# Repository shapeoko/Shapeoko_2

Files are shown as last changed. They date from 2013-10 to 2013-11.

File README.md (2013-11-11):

####Shapeoko is as much an idea as a physical machine.####

An idea that maybe there are people like me in the world. An idea that some people want a CNC machine but don't want to spend thousands of dollars to get one. An idea that maybe there are people who want a CNC machine, but don't necessarily know what they will make. An idea that maybe there are people who want a CNC machine but don't know how to use a CNC machine! An idea that maybe there are people who want to build something that was their own hands, but are not expert fabricators. An idea that a machine could be designed that was hackable, scalable, customizable, but doesn't require the re-invention of the wheel for each modification.

####An idea that maybe there was a different way to do CNC.####

Those ideas laid the foundation for Project Shapeoko. It was those ideas that [the community](http://www.shapeoko.com/forum) has built itself around. A community that started out as an email list and is now 1000+ active members strong, and growing everyday. A community that I wouldn't trade for anything.

Over the last two years the community has bounced ideas off each other, tested new ideas, discussed and debated trade-offs in various designs and improvements, and helped each other make a better machine. We are a pragmatic, positive bunch that hasn't taken it's eye off the main goal of the project: Let's do CNC a different way. Let's commoditize it, let's make it accessible to anyone who wants it, and lets give anyone a place where they can come learn, a place they can be part of a community, and place where the newest, greenest, most inexperienced person's ideas and suggestions are taken as seriously as anyone elses. 

Maybe the project is a physical Machine, but it's the community that keeps the project together. It's the community that keeps the project moving forward, and it's the community that is responsible for Shapeoko 2.

The culmination of all that, is what you see here. I'd like to introduce you to Shapeoko 2. Say hello.

Shapeoko 2

Shapeoko 2 has taken all of our design improvements and rolled them up into one thoughtful, low-cost, scalable, hackable, simple, beautifully designed package full of improvements over the v1 Release.

####Specifications:####
+ Working area is expanded to about 12" by 12" by 2.5"
+ Open front and back for loading in longer pieces of material
+ Dual-drive motors on the Y axis, standard
+ Double width Makerslide on the X axis for added stiffness and strength
+ Completely redesigned Z axis for added stiffness and easier tool changes
+ The wasteboard is now integrated with the machine
+ Re-engineered belt system keeps teeth cleaner and reduces skipping
+ Easier to assemble- put it together over a weekend or a couple of nights

#####To-Do List#####
- [x] Publish Original Design Files (Autodesk Inventor)
- [x] Publish Generic Design Files (STEP Format)
- [x] Publish Original Drawing Files (Autodesk Inventor)
- [ ] Publish Generic Drawing Files (PDF Format)
- [ ] Publish Generic Drawing Files (DXF Format)
- [X] Publish Assembly Instructions (Outline Format) - WIP
- [ ] Publish Formatted Assembly Instructions

_This is the beginning of this repository. Information will be added as it becomes available and time permits._

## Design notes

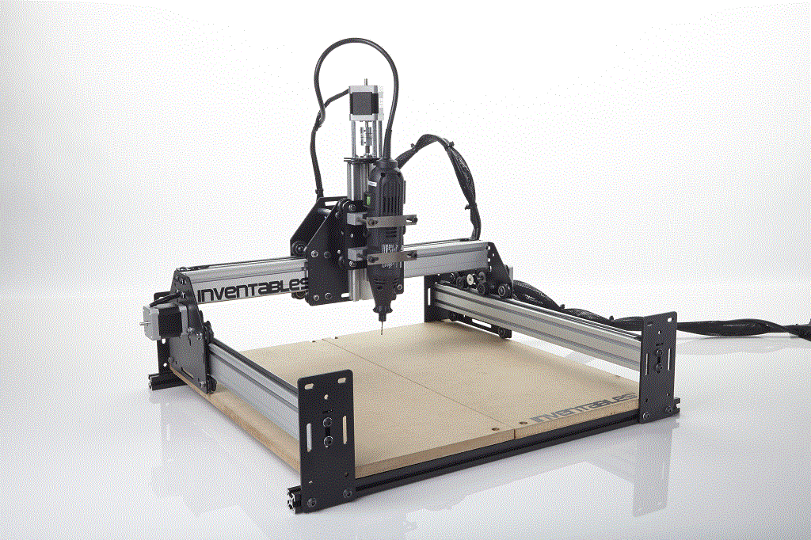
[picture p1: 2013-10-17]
Shapeoko_2.gif

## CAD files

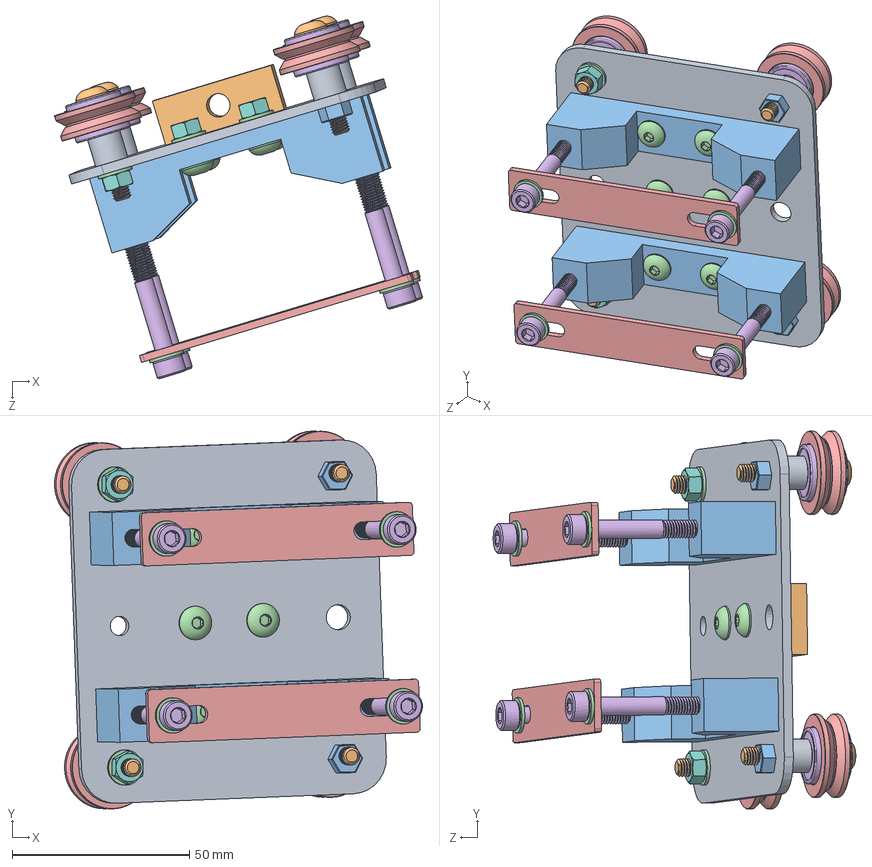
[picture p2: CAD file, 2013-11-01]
SolidWorks_Project/ASM_Zaxis_Trolly.SLDASM
104.0 x 106.7 x 102.4 mm
spindle_mount_plate
SM-M08
B18033 x 2
SM-TM x 2
SM-TM2 x 2
91290A260 x 4

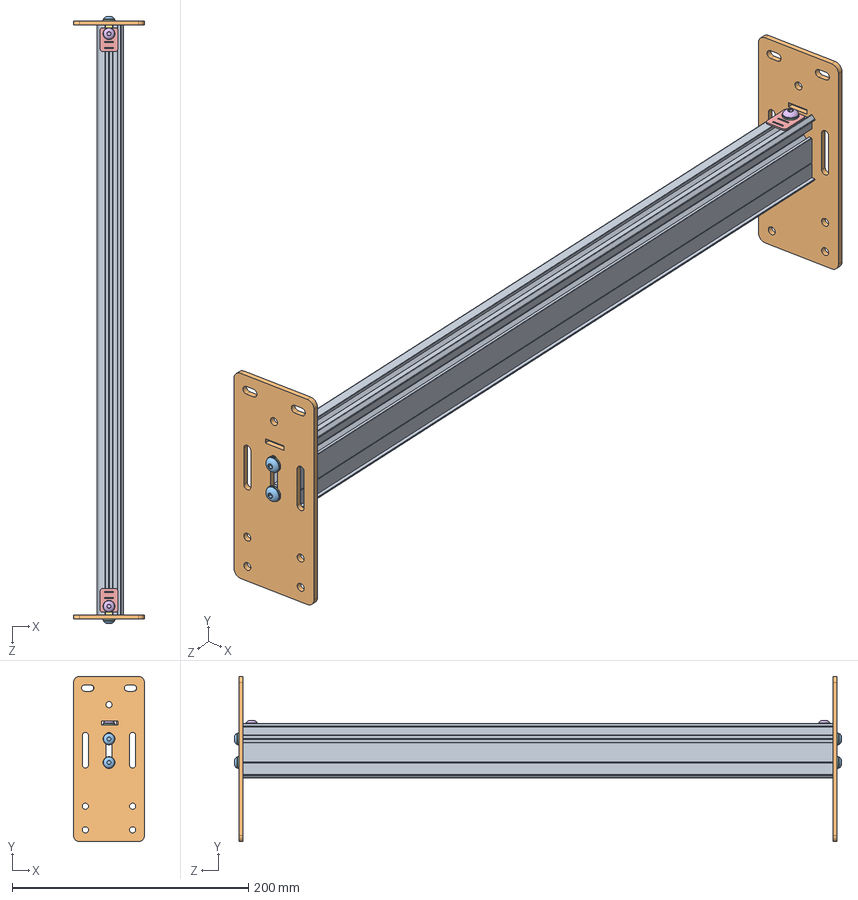
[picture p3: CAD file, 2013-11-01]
SolidWorks_Project/S2_Yaxis_Rail_500.sldasm
60.0 x 140.0 x 514.1 mm
25142-XX500
91239A222 x 2

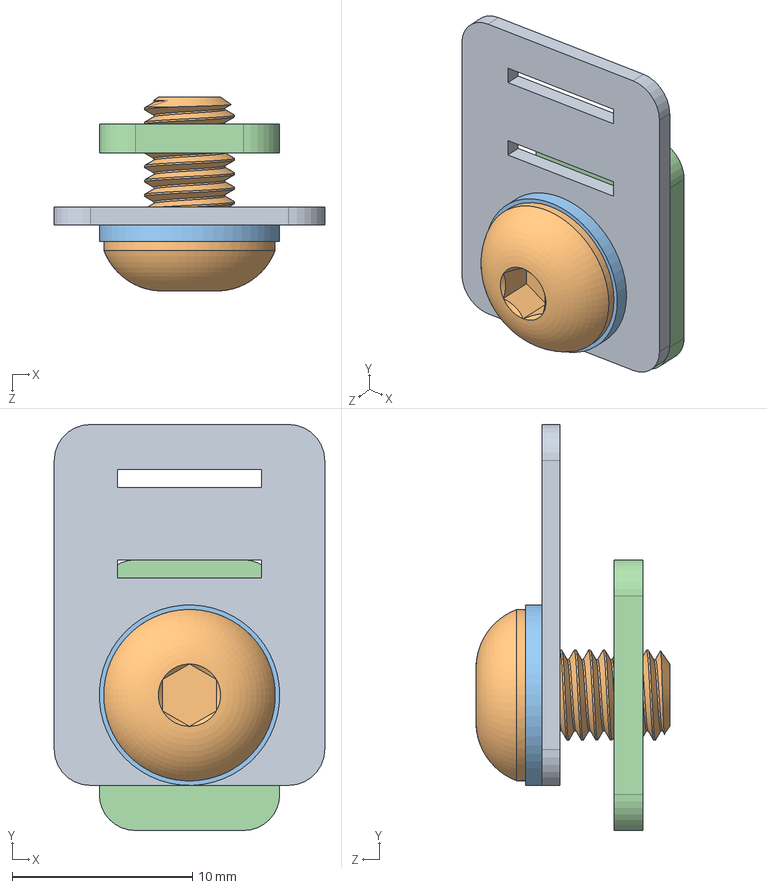
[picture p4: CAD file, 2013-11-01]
SolidWorks_Project/belt_clip_assembly.sldasm
15.0 x 22.5 x 10.7 mm
91239A222

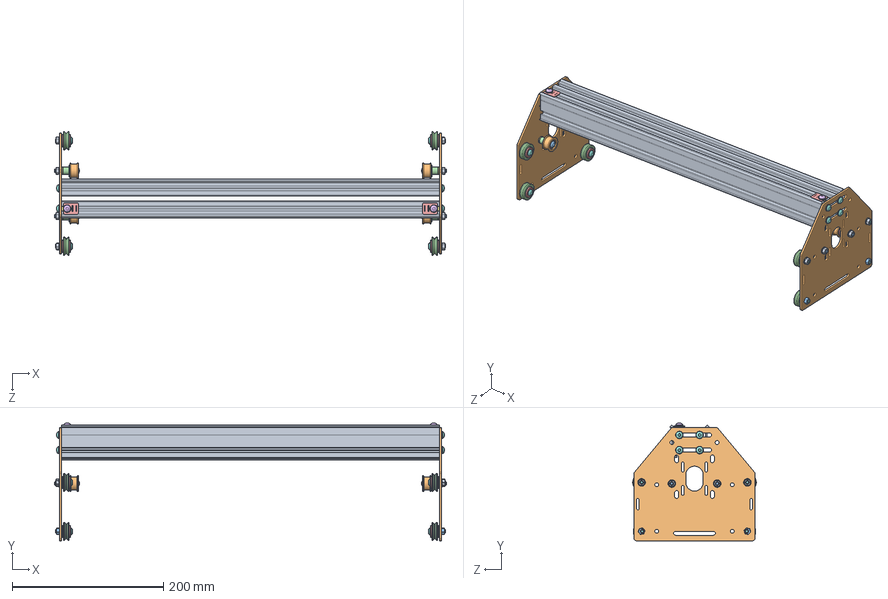
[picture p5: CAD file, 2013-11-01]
SolidWorks_Project/S2_Gantry_500.sldasm
518.5 x 155.6 x 163.5 mm
25142-XX500 x 2
B18033 x 4
91239A233 x 8
91239A222 x 2

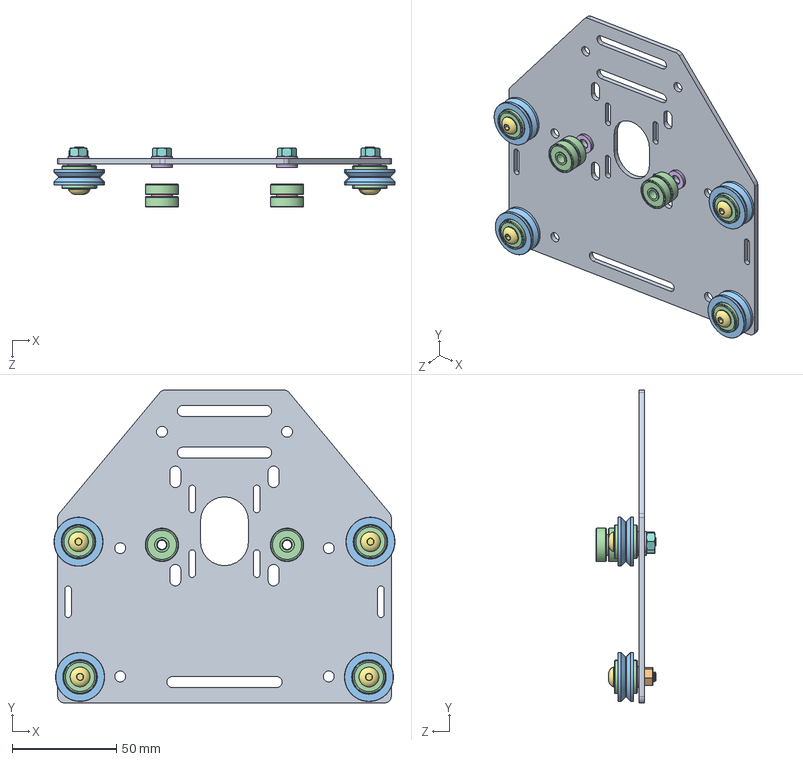
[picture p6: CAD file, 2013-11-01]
SolidWorks_Project/plate_assembly_stacked.sldasm
163.5 x 150.0 x 28.8 mm
B18033 x 2
91239A233 x 4

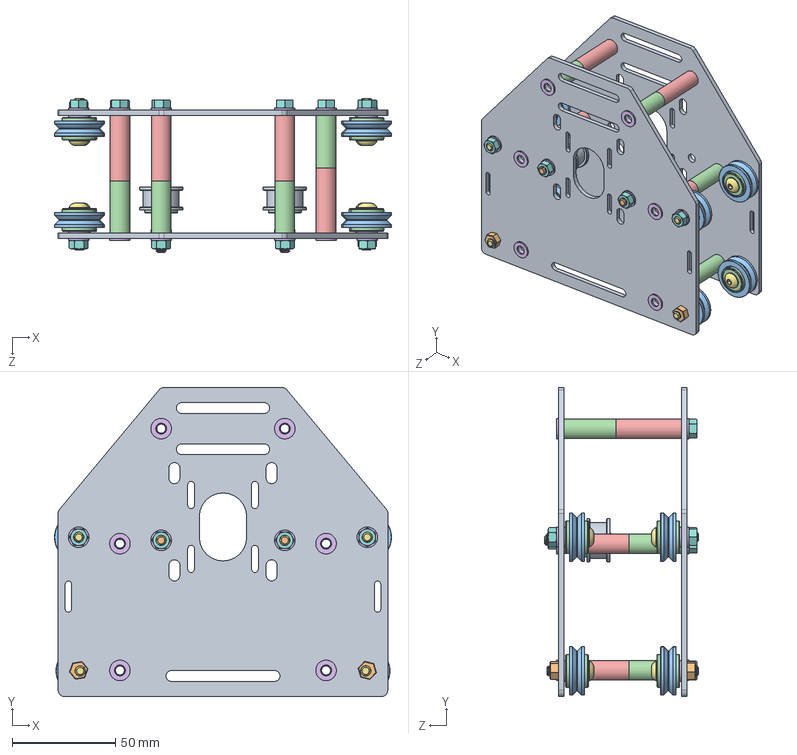
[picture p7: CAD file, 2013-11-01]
SolidWorks_Project/ASM_S2_Yaxis_Plates.SLDASM
163.5 x 150.0 x 74.5 mm
B18033 x 4
91239A233 x 8
AS38-12-64 x 6
AS38-12-80 x 6

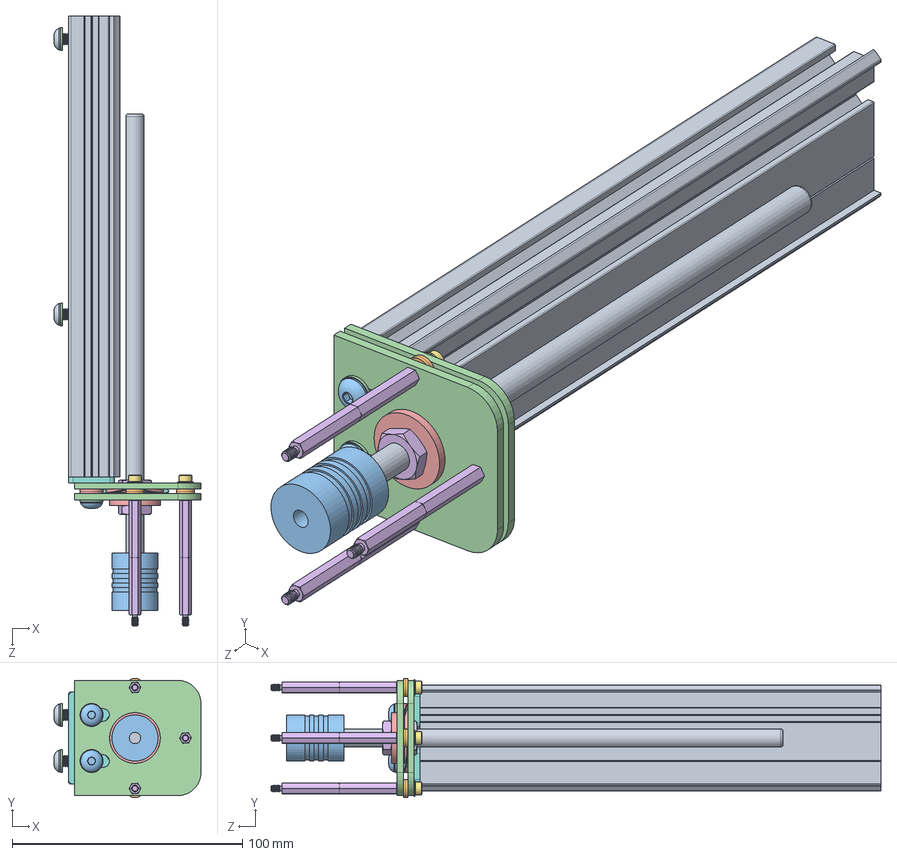
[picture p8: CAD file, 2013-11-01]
SolidWorks_Project/S2_Zaxis_500.sldasm
63.8 x 51.8 x 264.7 mm
z-mount_plates x 2
90695A040 x 2
z-axis shim
SM-H05
492-1101-ND x 6
91239A233 x 2
PSM5-01MM x 4
PSBS-50 x 3
9714K630

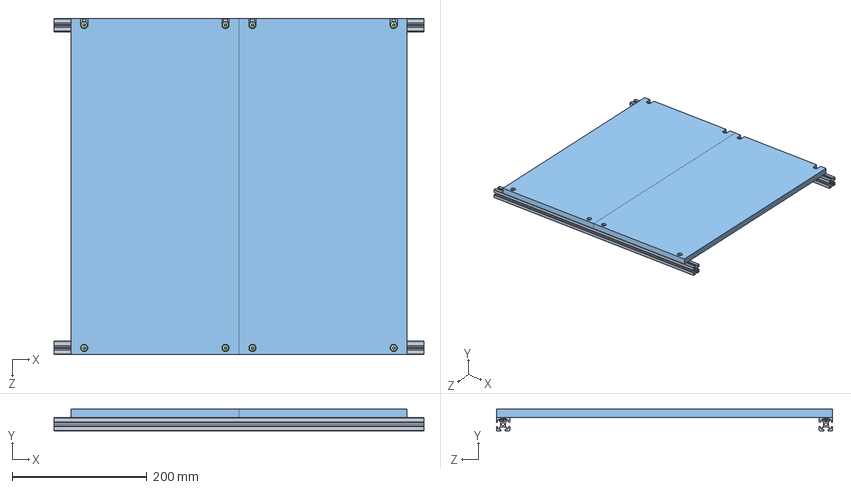
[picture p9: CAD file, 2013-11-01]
SolidWorks_Project/S2_Work_Area_500.sldasm
550.0 x 32.7 x 500.0 mm
two_part_wastebaord_500 x 2

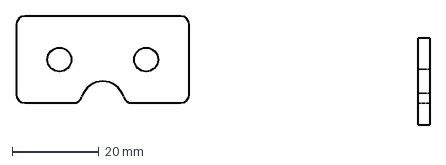
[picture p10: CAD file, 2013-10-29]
Drawings_DXF/SMZS-01.dxf
95.5 x 25.0 mm

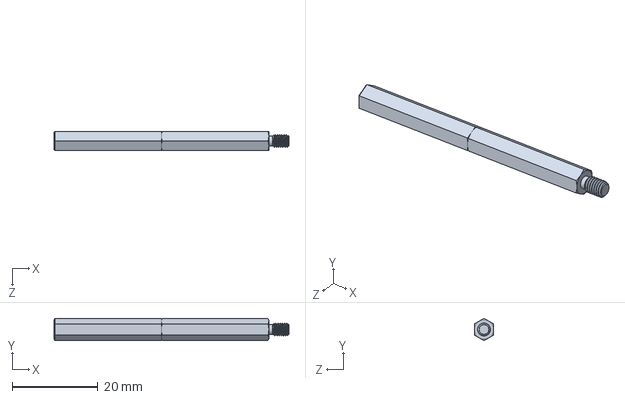
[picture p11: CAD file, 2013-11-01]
SolidWorks_Project/PSBS-50.sldprt
54.7 x 5.20 x 4.50 mm

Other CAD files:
SolidWorks_Project/SM-M08.sldprt
SolidWorks_Project/AS38-12-80.sldprt
SolidWorks_Project/PSM5-01MM.sldprt
SolidWorks_Project/SM-H05.sldprt
SolidWorks_Project/SM-TM.sldprt
SolidWorks_Project/z-axis shim.sldprt
SolidWorks_Project/z-mount_plates.sldprt
SolidWorks_Project/spindle_mount_plate.sldprt
Autodesk_Inventor_Project/25142-07.ipt
Autodesk_Inventor_Project/25142-XX500.ipt
Autodesk_Inventor_Project/25196-01.ipt
Autodesk_Inventor_Project/25197-01.ipt
Autodesk_Inventor_Project/25197-02.iam
Autodesk_Inventor_Project/25201-01.ipt
Autodesk_Inventor_Project/25202-01.ipt
Autodesk_Inventor_Project/25203-02.iam
Autodesk_Inventor_Project/25284-02.ipt
Autodesk_Inventor_Project/25285-10.ipt
Autodesk_Inventor_Project/25286-01.ipt
Autodesk_Inventor_Project/25286-02.ipt
Autodesk_Inventor_Project/25286-05.ipt
Autodesk_Inventor_Project/25287-02.ipt
Autodesk_Inventor_Project/25287-03.ipt
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

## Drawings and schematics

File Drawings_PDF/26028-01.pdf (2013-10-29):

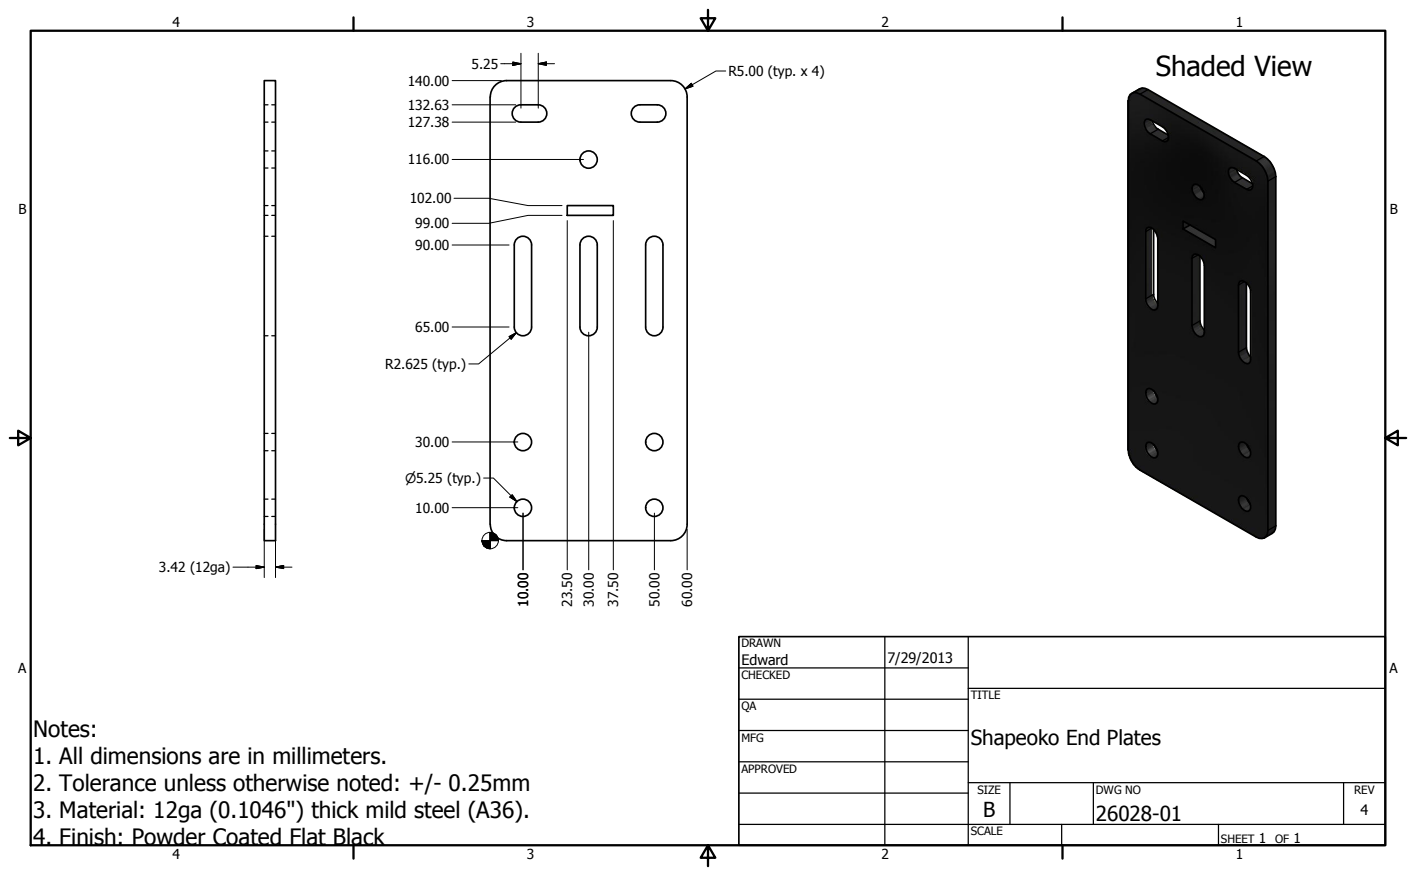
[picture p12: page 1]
SHEET 1 OF 1; DRAWN; CHECKED; MFG; APPROVED; Edward; DWG NO 26028-01; TITLE; SIZE B; SCALE; REV 4; P5.25 (typ.); R2.625 (typ.); R5.00 (typ. x 4); Shaded View

Notes:
1. All dimensions are in millimeters.
2. Tolerance unless otherwise noted: +/- 0.25mm
3. Material: 12ga (0.1046") thick mild steel (A36).
4. Finish: Powder Coated Flat Black

Shapeoko End Plates

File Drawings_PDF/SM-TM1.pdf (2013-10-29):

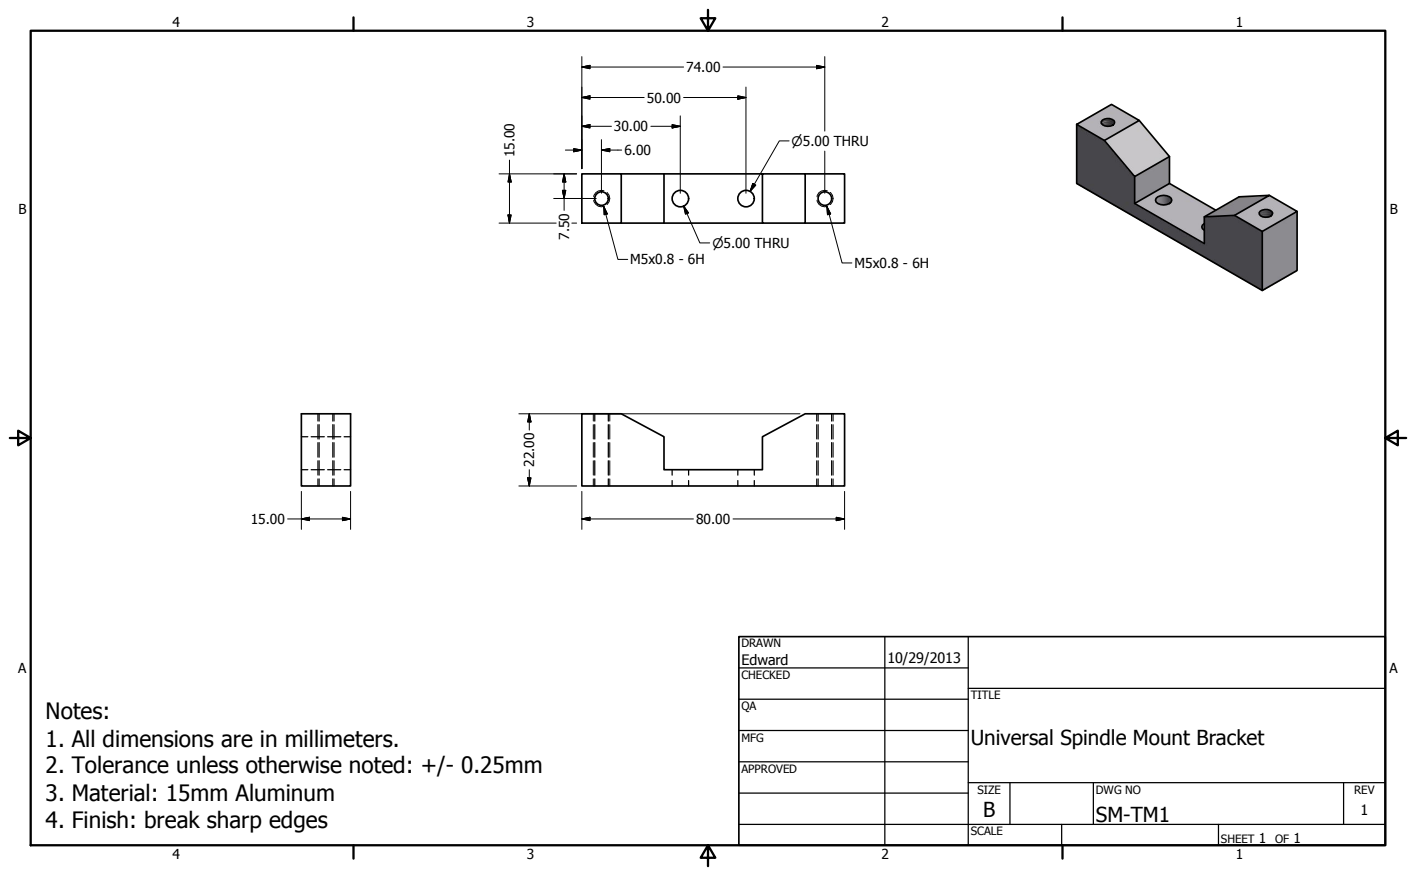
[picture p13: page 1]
SHEET 1 OF 1; DRAWN; CHECKED; MFG; APPROVED; Edward; DWG NO SM-TM1; TITLE; SIZE B; SCALE; REV 1; P5.00 THRU

Notes:
1. All dimensions are in millimeters.
2. Tolerance unless otherwise noted: +/- 0.25mm
3. Material: 15mm Aluminum
4. Finish: break sharp edges

Universal Spindle Mount Bracket

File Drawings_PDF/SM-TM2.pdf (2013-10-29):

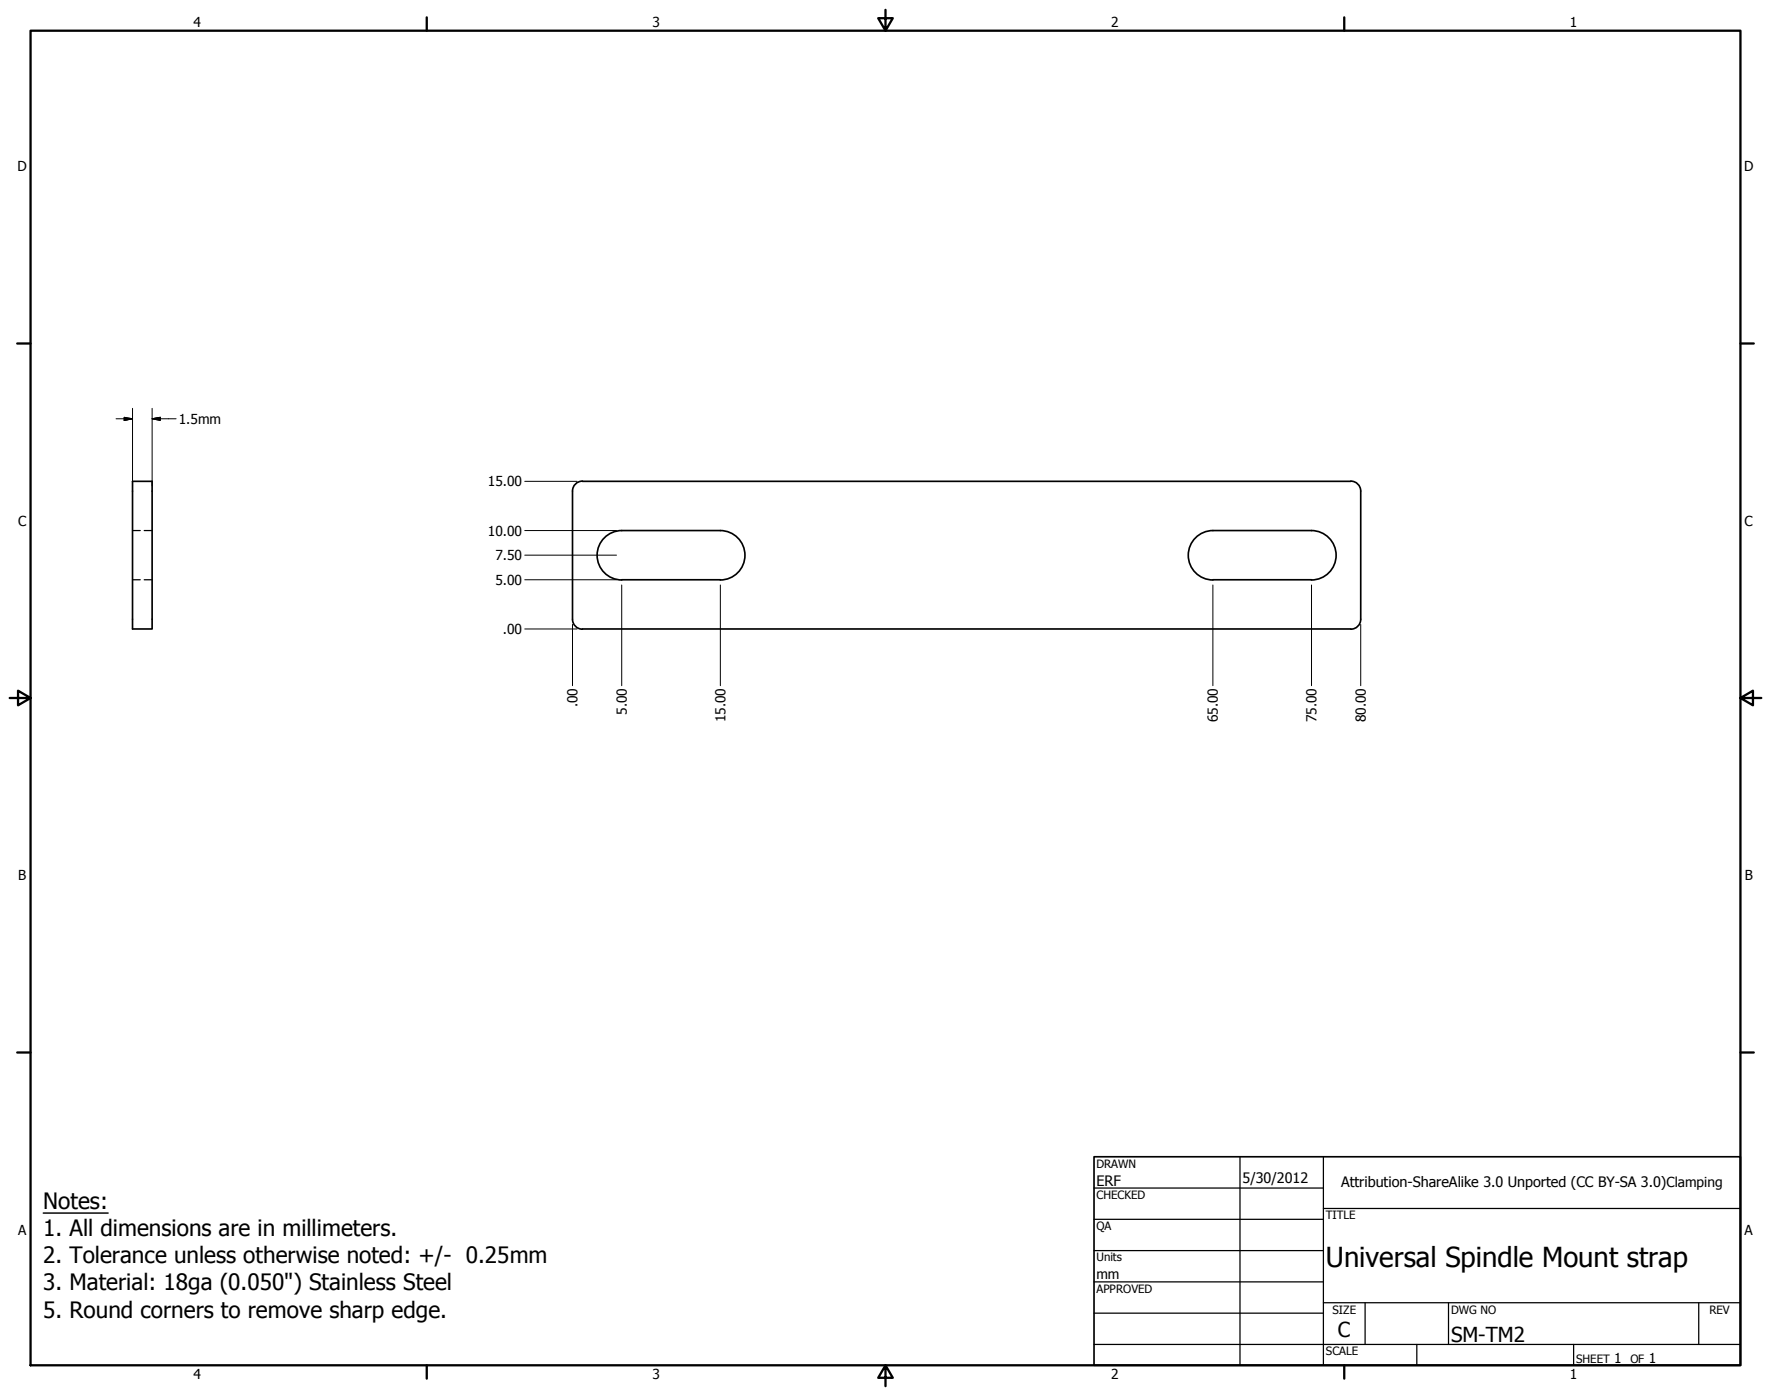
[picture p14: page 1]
SHEET 1 OF 1; DRAWN; CHECKED; Units; APPROVED; ERF; DWG NO SM-TM2; SIZE C; SCALE; REV

Attribution-ShareAlike 3.0 Unported (CC BY-SA 3.0)Clamping

Notes:
1. All dimensions are in millimeters.
2. Tolerance unless otherwise noted: +/- 0.25mm
3. Material: 18ga (0.050") Stainless Steel
5. Round corners to remove sharp edge.

TITLE
Universal Spindle Mount strap

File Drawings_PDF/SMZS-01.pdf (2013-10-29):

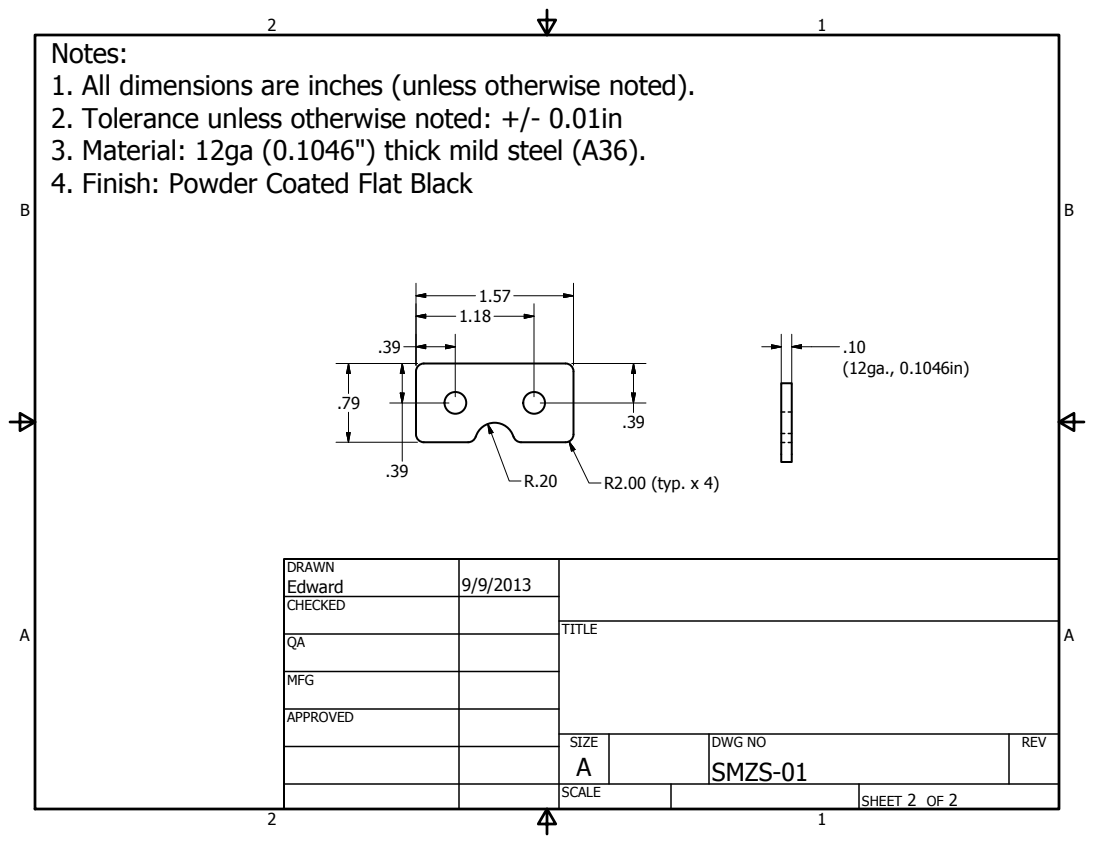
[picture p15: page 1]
SHEET 2 OF 2; DRAWN; CHECKED; MFG; APPROVED; Edward; DWG NO SMZS-01; TITLE; SIZE A; SCALE; REV; R2.00 (typ. x 4)

Notes:
1. All dimensions are inches (unless otherwise noted).
2. Tolerance unless otherwise noted: +/- 0.01in
3. Material: 12ga (0.1046") thick mild steel (A36).
4. Finish: Powder Coated Flat Black

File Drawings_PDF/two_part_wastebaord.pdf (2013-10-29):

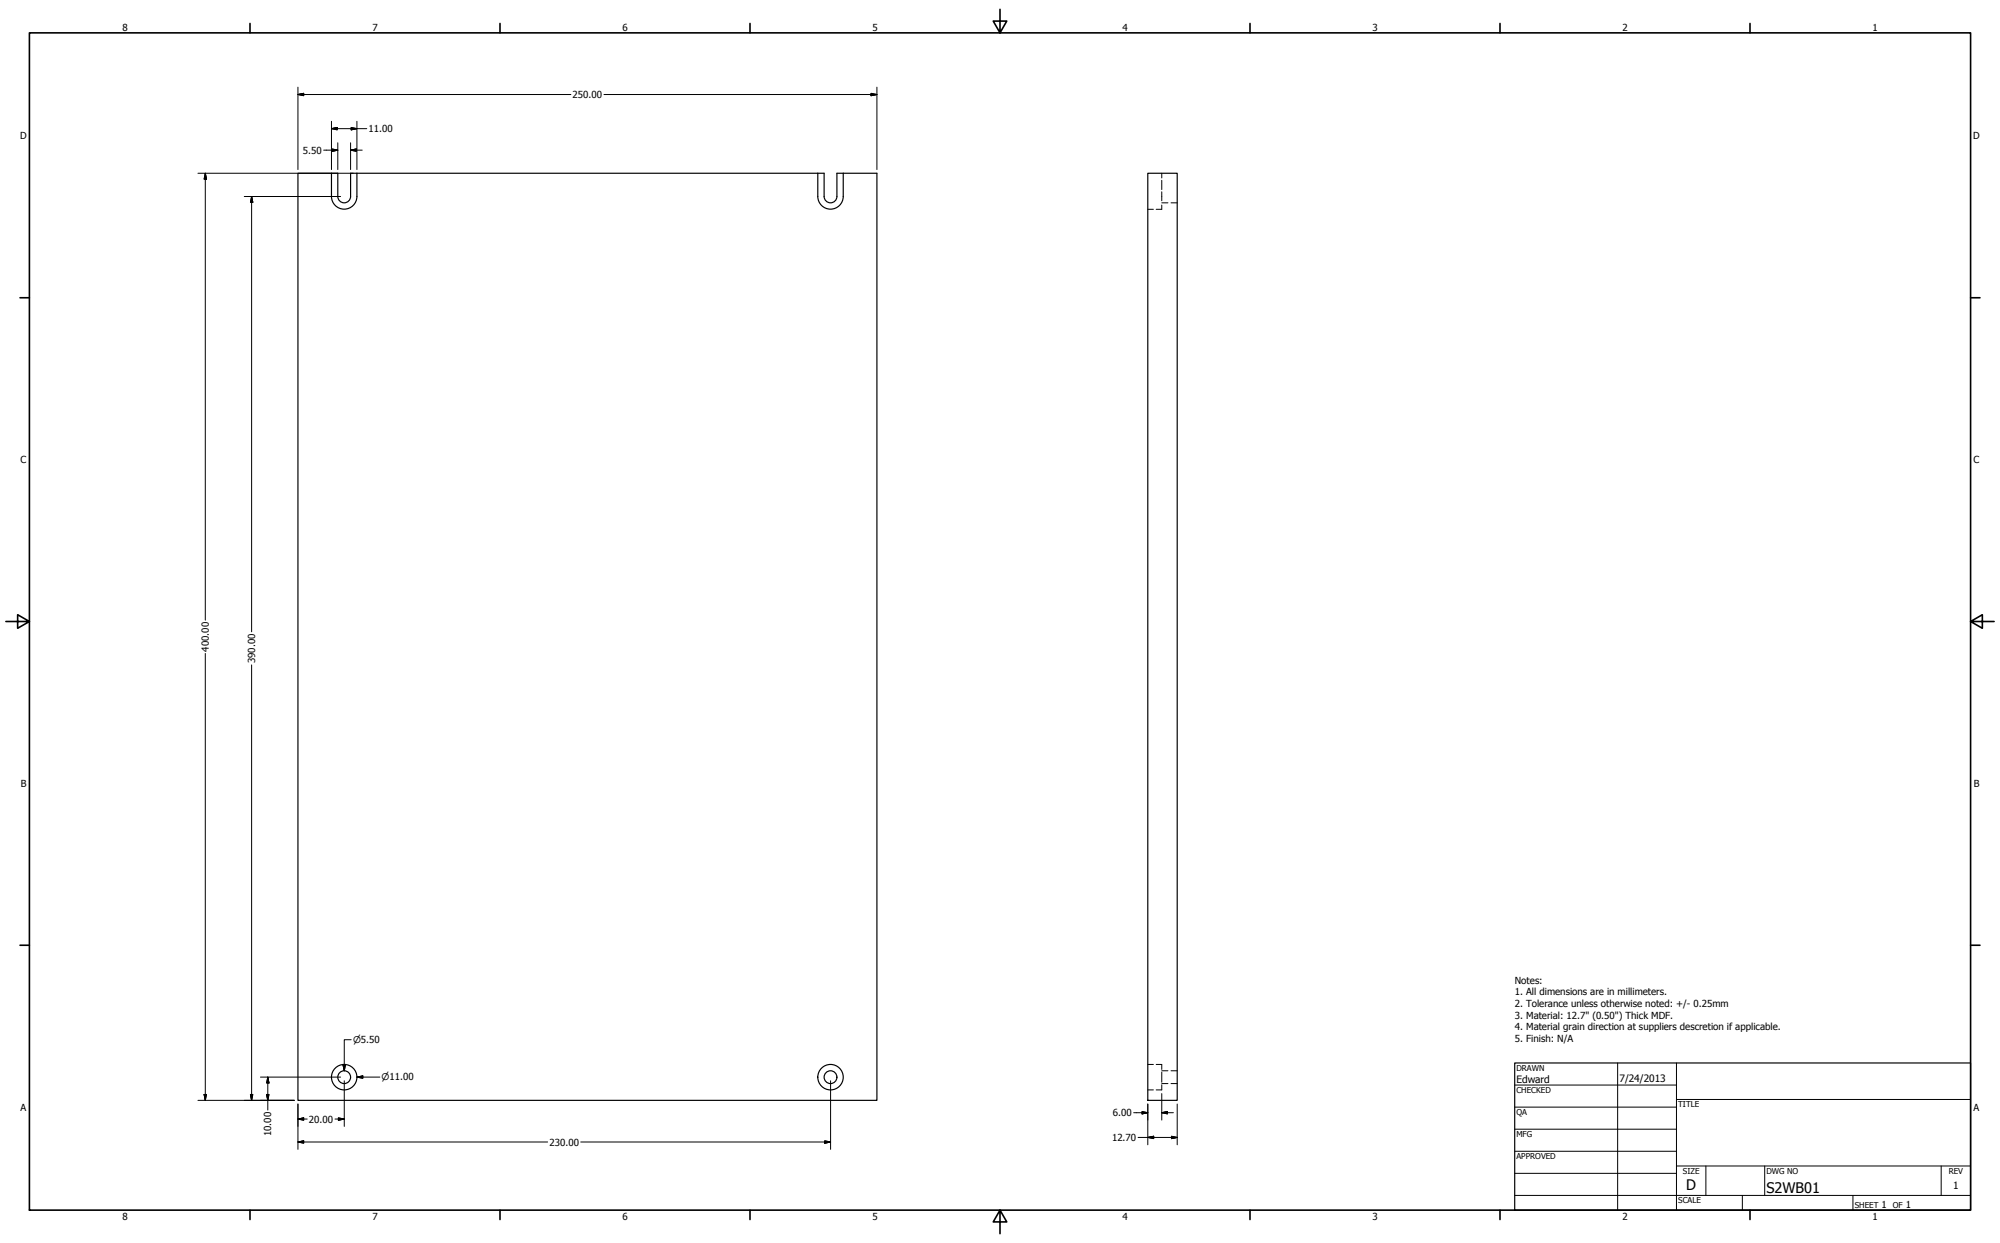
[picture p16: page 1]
SHEET 1 OF 1; DRAWN; CHECKED; MFG; APPROVED; Edward; DWG NO S2WB01; TITLE; SIZE D; SCALE; REV 1

Notes:
1. All dimensions are in millimeters.
2. Tolerance unless otherwise noted: +/- 0.25mm
3. Material: 12.7" (0.50") Thick MDF.
4. Material grain direction at suppliers descretion if applicable.
5. Finish: N/A

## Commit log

2013-10-17 Cleaning Up Filenames
    [Shapeoko_2.iam]
2013-10-17 Changed Pattern
    Pattern was reflecting old design. Updated to correct spacing.
    [S2_Work_Area_500.iam, Shapeoko_2.iam]
2013-10-17 Cleaning up filenames
    making part numbers consistent.
    [AS38-12-80.ipt, S2_Zaxis_500.iam, Shapeoko_2.iam]
2013-10-17 Organizing directory structure
    Moving projects into own folder.
    [25142-07.ipt, 25142-XX500.ipt, 25196-01.ipt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]
2013-10-29 initial drawing commit
    [26028-01.idw, 26029-01.idw, S2SM-01.idw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]
2013-11-01 adding solidworks version of Shapeoko_2
    Submitted by community user. This is a full SolidWorks assembly, with
    part files, constraints, and proper assembly file.
    [25142-07.sldprt, 25142-XX500.sldprt, 25196-01.sldprt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]
2013-11-11 adding arduino troubleshooting template
2013-11-11 adding stepper troubleshooting page
2013-11-15 saved model, no change
    [Shapeoko_2.iam]
